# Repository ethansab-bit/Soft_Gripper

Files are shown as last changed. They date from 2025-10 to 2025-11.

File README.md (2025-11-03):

# Whole-Body Proprioceptive Morphing: A Modular Soft Gripper for Robust Cross-Scale Grasping

Official code repository for the paper:  
**"Whole-Body Proprioceptive Morphing: A Modular Soft Gripper for Robust Cross-Scale Grasping"**

## Authors

**Dong Heon Han¹, Xiaohao Xu²†, Yuxi Chen¹, Yusheng Zhou², Xinqi Zhang¹, Jiaqi Wang², Daniel Bruder¹, Xiaonan Huang²***  

¹ *Mechanical Engineering Department, University of Michigan – Ann Arbor, Ann Arbor, MI, USA*  
² *Robotics Department, University of Michigan – Ann Arbor, Ann Arbor, MI, USA*  

† *Project Lead* | * Corresponding Author  

**Emails:**  
- (dongheon, ethansab, dadaaa, dbruder)@umich.edu
- (xiaohaox, yszhou, wangjq, xiaonanh)@umich.edu



## Overview
This repository provides the control and communication code for the modular soft gripper system described in the paper.
The system integrates Arduino-based low-level actuation and a Python control interface for proprioceptive feedback and grasp modulation.

## Repository Structure
```bash
main/
├── Gripper_CAD/                    # CAD files
├── Gripper_FullCode/
│   └── Gripper_FullCode.ino        # Firmware controlling the modular soft gripper
├── GripperControl.py               # Main Python UI and control logic
├── serial_controller.py            # Handles serial communication with Arduino
├── uipic.png                       # UI illustration
├── UserInterfaceDemo.png
├── Schematic_Gripper.png
├── requirements.txt
└── README.md
```

## Clone the Repository
To download or clone this repository:
### Option 1 — Using HTTPS
```bash
git clone https://github.com/ethansab-bit/Soft_Gripper.git
```
### Option 2 — Download ZIP
Click the **Code → Download ZIP** button on GitHub, then unzip the project folder locally.

## Requirements
### Python Environment
- Python ≥ 3.8
- Install required dependencies:
  ```bash
  pip install -r requirements.txt
  ```
### Arduino Environment
- Arduino IDE ≥ 2.0
- Required Libraries:
  1. [Adafruit LPS35HW Library](https://github.com/adafruit/Adafruit_LPS35HW) (Provides the   `Adafruit_LPS35HW.h` header used for pressure sensing)
  2. [Adafruit Sensor Library](https://github.com/adafruit/Adafruit_Sensor) (Dependency required by LPS35HW library)
  
  To install:
    1. Open **Arduino IDE**
    2. Go to **Tools → Manage Libraries...**
    3. Search for **“Adafruit LPS35HW”**
    4. Click **Install** (this will automatically install its dependencies)

## Usage
### System Wiring
The control system requires the following electric devices:
  - Arduino Mega2560 Control Board × 1
  - L298N Motor Driver × 3
  - X605LF Valve × 10
  - LPS3X Pressure Sensor × 4
  - Bending Sensor × 4

The **Arduino Mega2560** should remain connected to the computer **at all times** for communication and control.
All **L298N motor drivers** and bending sensors must be powered by a **5 V** source.

Each bending sensor should be connected in series with a **15 kΩ resistor** to ground. The junction point between the sensor and the resistor should be wired to one of the **analog input ports (A0–A15)** on the Mega2560.

All **VCC pins** of the LPS3X pressure sensors should be connected to the **3.3 V output** on the Mega2560.

The complete wiring layout is illustrated in the diagram below:
<p align="center">
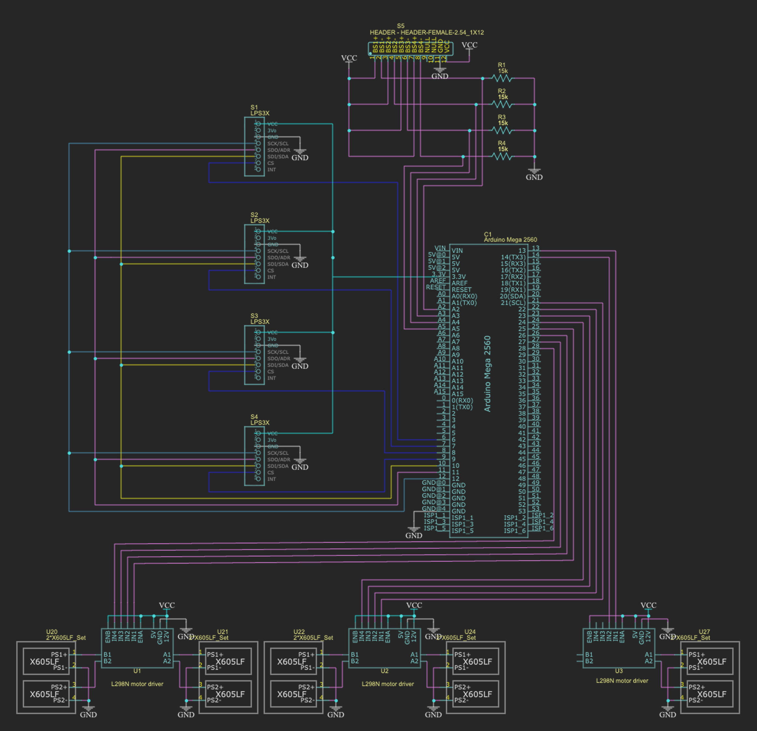
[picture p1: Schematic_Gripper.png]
  
</p>

### Upload the Arduino Code
1. Open `Gripper_FullCode/Gripper_FullCode.ino` in **Arduino IDE**
2. Ensure the **Adafruit_LPS35HW** and **Adafruit_Sensor** libraries are installed
3. Select the correct **Board** and **Port**
4. Click **Upload**

**Notice**: The `Gripper_FullCode.ino` file **must remain inside its folder with the same name** (`Gripper_FullCode/`). Otherwise, the Arduino IDE will not be able to locate dependencies and compile the code.

### Run the Python Control Interface
```bash
python GripperControl.py --port COM4
```
This command launches the UI for controlling the gripper and visualizing proprioceptive (pressure-based) feedback. Make sure to **replace** `COM4` **with the serial port corresponding to your Arduino Control Board**. You can check the active serial port under **Tools → Port** in the **Arduino IDE**. If `--port ...` is omitted, the program will use the default port setting `COM4`.

**Notice**: Before running the Python control program, make sure to **close the Serial Monitor** in the Arduino IDE (or any other application accessing the serial port). **Only one program can use the serial connection at a time**.

### Control Interface Operation
The graphical user interface (GUI) allows users to control and monitor each pneumatic actuator of the soft gripper in real time.  
Each actuator’s target and measured pressure (in hPa) are displayed along with control sliders and state indicators.
<p align="center">
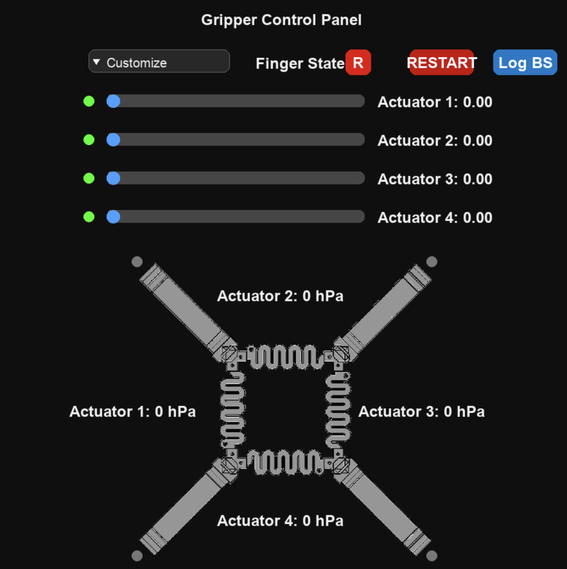
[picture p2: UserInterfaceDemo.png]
  
</p>
Users can:

  - Adjust actuator length using the on-screen sliders (0.00-1.00 extension)
  - Observe real-time sensor readings from **LPS35HW** pressure sensors  
  - Control the gripper finger states (`Finger State` button, `R` for **Release**, `G` for **Gripped**)  
  - Log the data from four bending sensors (`Log BS`). The data will be stored in the same directory as `bend_log.txt`.
  - Recalibrate the actuator (`Restart`). The system will release all air pressure in actuators and fingers and automatically recalibrate to atmospheric pressure within a few seconds.

## CAD Files
All CAD resources for the soft gripper are organized within the repository: Soft_Gripper / Gripper_CAD

## Paper
arxiv: https://arxiv.org/abs/2510.27666

---

## License
This project is licensed under the [MIT License](https://opensource.org/licenses/MIT).

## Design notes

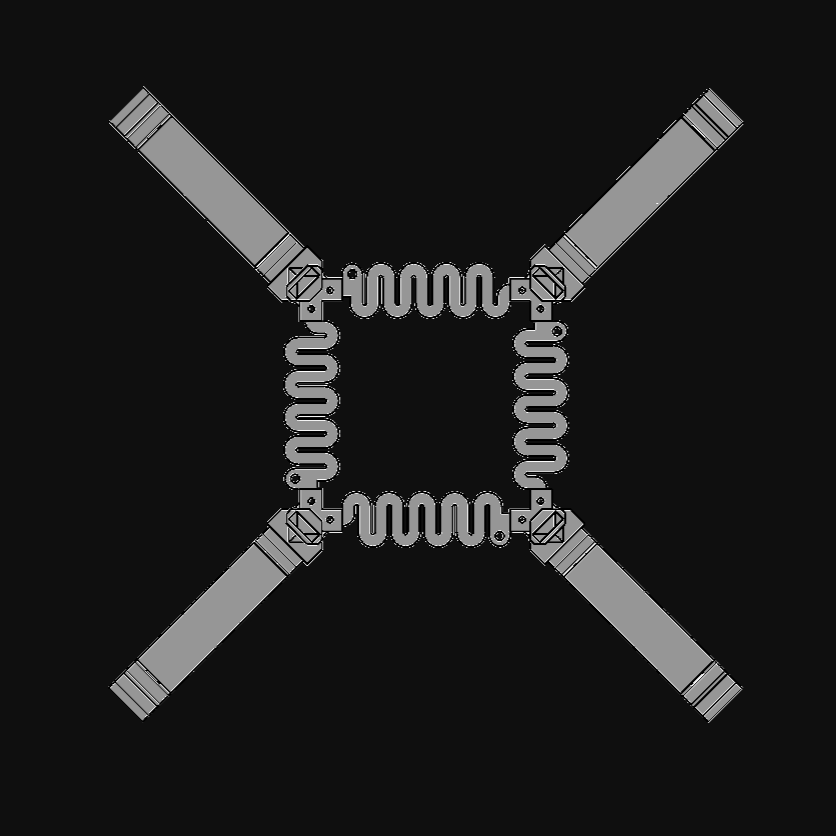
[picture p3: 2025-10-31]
uipic.png

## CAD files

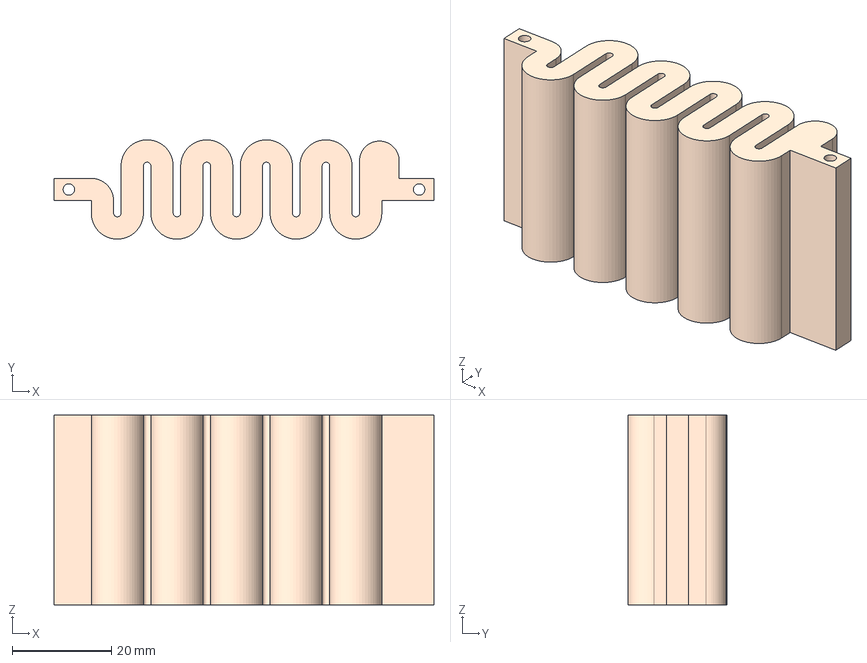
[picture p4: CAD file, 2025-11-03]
Gripper_CAD/Palm.step
76.5 x 20.0 x 38.2 mm

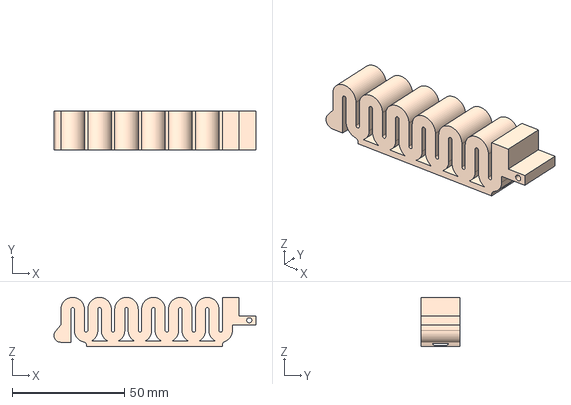
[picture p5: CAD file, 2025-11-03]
Gripper_CAD/Finger.step
90.1 x 17.5 x 22.0 mm

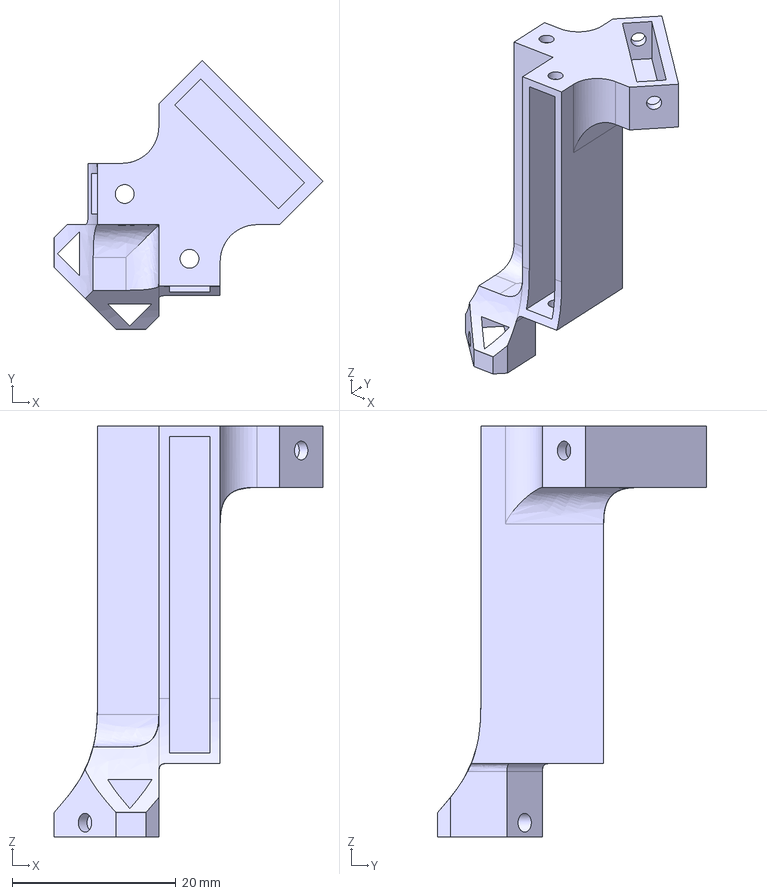
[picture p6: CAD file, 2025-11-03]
Gripper_CAD/bodyConnector.step
32.9 x 32.9 x 50.2 mm

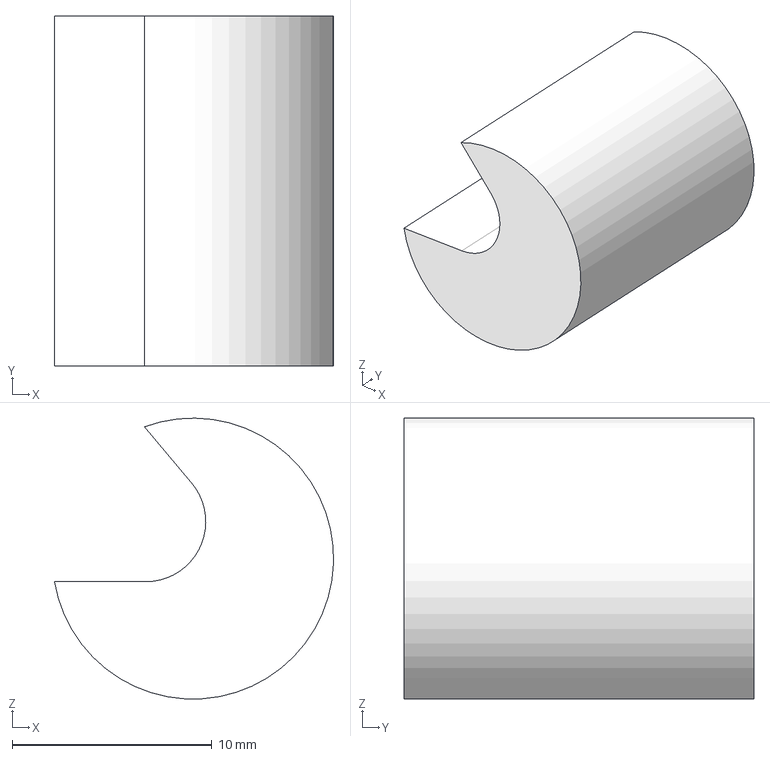
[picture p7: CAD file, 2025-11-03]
Gripper_CAD/Finger Tip.step
14.0 x 17.5 x 14.0 mm

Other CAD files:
Gripper_CAD/Finger Tip.stl
Gripper_CAD/bodyConnector.stl

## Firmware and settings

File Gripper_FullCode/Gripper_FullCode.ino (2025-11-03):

#include <Adafruit_LPS35HW.h>
#include <SPI.h>
#include <math.h>

// Port Declaration
#define SCK 12
#define SDO 11
#define SDI 10
const int CSP[4] = {6, 7, 8, 9};

const int BS[4] = {A2, A3, A4, A5};

const int ActIn[4]  = {22, 24, 26, 28};
const int ActOut[4] = {23, 25, 27, 29};

const int FinIn = 13;
const int FinOut = 14;

// Pressure Sensor
Adafruit_LPS35HW preSensor[4] = {Adafruit_LPS35HW(), Adafruit_LPS35HW(), Adafruit_LPS35HW(), Adafruit_LPS35HW()};

// Time Variable
unsigned long curTime;
unsigned long preTime;
float dt = 0;
float cycleLength = 100;
unsigned long startCycle = 0;
const int finChargeCycle = 10;
const float finChargeProp = 0.5;

// Pressure Variable
float targetPre[4] = {0, 0, 0, 0};
float currentPre[4] = {0, 0 ,0 ,0};
float errorPre[4] = {0, 0, 0, 0};
float atmPre = 0;

// Input Variable
float targetActState[4] = {0, 0, 0, 0};
bool targetFinState = false;

// Output Variable
int gripFlag[4] = {0, 0, 0, 0};
bool stopFlag[4] = {true, true, true, true};
const int gripRange[4] = {82, 46, 47, 23};
const int gripLowLimit[4] = {91, 29, 119, 47};
const float gripThrehold[4] = {.95, .60, .60, .90};

// PID Constant
const float Kp = 0.001;
const float Ki = 0.000003;
const float Kd = 0.000008;

// Control Constant
const float deadLimit = 0.03;
float interval = 1076.0230;

// PID Variable
float integral[4] = {0, 0, 0, 0};
float derivative[4] ={0, 0, 0, 0};
float error[4] = {0, 0, 0, 0};
float preError[4] = {0, 0, 0, 0};
float score[4] = {0, 0, 0, 0};

// Function Declaration
void ReadInput();
void InitialState();
void Len2Pre();
void readCurPre();
void CalcTime();
void CalcPID();
void ControlValve();
void PrintInfo();

void setup() {
  // put your setup code here, to run once:
  Serial.begin(9600); 

  // Initiate Pressure Sensor
  for (int i = 0; i < 4; i++) {
    if (!preSensor[i].begin_SPI(CSP[i], SCK, SDO, SDI)) {
      Serial.print("Invalid Pressure Sensor #");
      Serial.println(i);
      while(1);
    }
  }

  // Initaite the Valve
  for (int i = 0; i < 4; i++) {
    pinMode(ActIn[i], OUTPUT);
    pinMode(ActOut[i], OUTPUT);
  }
  pinMode(FinIn, OUTPUT);
  pinMode(FinOut, OUTPUT);

  // Initiate Time
  curTime = millis();
  preTime = millis();

  InitialState();
}


void loop() {
  // put your main code here, to run repeatedly:
  ReadInput();
  Len2Pre();
  readCurPre();
  readGripFlag();
  CalcTime();
  CalcPID();
  ControlValve();
  PrintInfo();
}

void ReadInput() {
  // Read input from the serial, changing length by "l1 l2 l3 l4", constrol finger by "G" or "R", restart by "S"
  if (Serial.available() > 0) {
    String input = Serial.readStringUntil('\n');
    input.trim();

    if (input == "s" || input == "S") {
      for (int i = 0; i < 4; i++) {
        targetActState[i] = 0;
      }
      targetFinState = false;
      InitialState();
      return;
    }

    if (input == "g" || input == "G") {
      targetFinState = true;
    } else if (input == "r" || input == "R") {
      targetFinState = false;
    }

    float temp[4];
    int index = 0;

    int lastSpace = -1;
    for (int i = 0; i < input.length(); i++) {
      if (input.charAt(i) == ' ' || i == input.length() - 1) {
        int endIdx = (input.charAt(i) == ' ') ? i : i + 1;
        String numStr = input.substring(lastSpace + 1, endIdx);
        numStr.trim();
        if (index < 4) {
          temp[index] = numStr.toFloat();
          index++;
        }
        lastSpace = i;
      }
    }

    if (index == 4) {
      for (int i = 0; i < 4; i++) {
        targetActState[i] = constrain(temp[i], 0.0, 1.2);
      }
    } else {
      Serial.println("Invalid input. Please enter 4 numbers.");
    }
  }
}

void InitialState() {
  // Release all the pressure in fingers & actuators
  for (int i = 0; i < 4; i++) {
    digitalWrite(ActIn[i], LOW);
    digitalWrite(ActOut[i], HIGH);
    delay(1000);
  }
  digitalWrite(FinIn, LOW);
  digitalWrite(FinOut, HIGH);
  delay(1000);

  // Measure & Reset the atmosphere pressure
  float sumPre = 0;
  for (int i = 0; i < 4; i++) {
    for (int j = 0; j < 10; j++) {
      sumPre += preSensor[i].readPressure();
    }
  }
  atmPre = sumPre / 40;
  delay(500);
}

void Len2Pre() {
  // Transfer the length proportion into pressure
  
  for (int i = 0; i < 4; i++) {
    if (targetActState[i] == 0) {
      targetPre[i] = 0;
      continue;
    }
    float targetLength = 70 * (1 + targetActState[i]);
    targetPre[i] = 0.002 * targetLength * targetLength * targetLength - 0.6508 * targetLength * targetLength + 75.6529 * targetLength - 1798.7 - atmPre;
  }
}

void readCurPre() {
  for (int i = 0; i < 4; i++) {
    currentPre[i] = preSensor[i].readPressure() - atmPre;
  }
}

void readGripFlag() {
  if (targetFinState) {
    for (int i = 0; i < 4; i++) {
      if ((float)(analogRead(BS[i]) - gripLowLimit[i])/(float)gripRange[i] < gripThrehold[i]) {
        gripFlag[i] = 1;
      } else {
        gripFlag[i] = -1;
      }
    }
  } else {
    for (int i = 0; i < 4; i++) {
      gripFlag[i] = 0;
    }
  }
}

void CalcTime() {
  // Calculate the derivative time and renew curTime & preTime
  curTime = millis();
  dt = (curTime - preTime) / 1000.0;
  preTime = curTime;
}

void CalcPID() {
  // Calculate PID with constant and variable and return a estimate score from -1 to 1
  for (int i = 0; i < 4; i++) {
    error[i] = targetPre[i] - currentPre[i];
    integral[i] += error[i] * dt;
    derivative[i] = (error[i] - preError[i]) / dt;
    preError[i] = error[i];
    score[i] = constrain(Kp * error[i] + Ki * integral[i] + Kd * derivative[i], -1, 1);
  }
}

void ControlValve() {
  // Control the actuators and fingers using the PID control variables
  unsigned long curTimeTemp = millis();
  unsigned long curCycleTime = curTimeTemp - startCycle;

  if (curCycleTime >= cycleLength) {
    startCycle = curTimeTemp;
    curCycleTime = 0;
  }

  for (int i = 0; i < 4; i++) {
    if (score[i] > deadLimit && curCycleTime < fabs(score[i]) * cycleLength) {
      digitalWrite(ActIn[i], HIGH);
      digitalWrite(ActOut[i], LOW);
      stopFlag[i] = false;
    } else if (score[i] < -deadLimit && curCycleTime < fabs(score[i]) * cycleLength) {
      digitalWrite(ActIn[i], LOW);
      digitalWrite(ActOut[i], HIGH);
      stopFlag[i] = false;
    } else {
      digitalWrite(ActIn[i], LOW);
      digitalWrite(ActOut[i], LOW);
      if (score[i] >= -deadLimit && score[i] <= deadLimit) {
        integral[i] = 0;
        stopFlag[i] = true;
      }
    }
  }

  if (targetFinState) {
    digitalWrite(FinIn, HIGH);
    digitalWrite(FinOut, LOW);
  } else {
    digitalWrite(FinIn, LOW);
    digitalWrite(FinOut, HIGH);
  }

}

void PrintInfo() {
  // Print the state of the gripper
  for (int i = 0; i < 4; i++) {
    Serial.print(currentPre[i] + atmPre);
    Serial.print(" ");
  }
  for (int i = 0; i < 4; i++) {
    if (stopFlag[i]) {
      Serial.print("T");
    } else {
      Serial.print("F");
    }
    Serial.print(" ");
  }
  for (int i = 0; i < 4; i++) {
    Serial.print(gripFlag[i]);
    Serial.print(" ");
  }
  for (int i = 0; i < 4; i++) {
      Serial.print(analogRead(BS[i]));
      Serial.print(" ");
  }
  Serial.println();

}

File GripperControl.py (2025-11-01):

import pygame
import pygame.gfxdraw
import math
import os
import sys
import time
import argparse
from serial_controller import SerialController

def main():
    parser = argparse.ArgumentParser(description="Gripper Control Panel")
    parser.add_argument("--port", type=str, default="COM4",
                        help="Serial port for Arduino connection (e.g. COM3 or /dev/cu.usbmodem101)")
    args = parser.parse_args()

    sc = SerialController(args.port)
    print(f"Connected to serial port: {args.port}")

# ===== Color Theme =====
COLOR_BG         = (15, 15, 15)
COLOR_CARD_BG    = (30, 30, 30)
COLOR_TRACK      = (70, 70, 70)
COLOR_KNOB       = (60, 160, 255)
COLOR_TRACK_HL   = (120, 120, 120)
COLOR_TEXT       = (240, 240, 240)

COLOR_BTN_G      = (0, 168, 84)
COLOR_BTN_R      = (230, 0, 0)
COLOR_BTN_LABEL  = (255, 255, 255)

MODEL_BTN_BG     = (40, 40, 40)
MODEL_BTN_BORDER = (100, 100, 100)
MODEL_BTN_TEXT   = (240, 240, 240)

COLOR_PANEL_BG           = (45, 45, 45)
COLOR_PANEL_ITEM         = (60, 60, 60)
COLOR_PANEL_ITEM_HOVER   = (80, 80, 80)

COLOR_IND_X = (120, 120, 120)   
COLOR_IND_T = (0, 255, 0)     
COLOR_IND_F = (255, 0, 0)     

# ===== UI POSITION =====
WIN_W, WIN_H = 900, 900
SLIDER_X, SLIDER_W = 180, 400
SLIDER_TOP, SLIDER_SPACING, SLIDER_H = 150, 60, 20
ACTPOS = [[100, 630], [330, 450], [550, 630], [330, 800]]

BEND_BTN_RECT = pygame.Rect(780, 80, 100, 40)
bend_pressed = False
logging_bend = False
bend_file = None


KNOB_MARGIN = 8

FLAG_BOX_RECT = pygame.Rect(550, 80, 40, 40)
MODEL_BTN_RECT = pygame.Rect(150, 80, 220, 36)
MODEL_ITEM_H = 30
MODEL_DROPDOWN_X = MODEL_BTN_RECT.x
MODEL_DROPDOWN_Y = MODEL_BTN_RECT.bottom + 4
MODEL_DROPDOWN_W = MODEL_BTN_RECT.width
STOP_BTN_RECT = pygame.Rect(650, 80, 100, 40)

GRIP_CENTER = [[225, 410], [684, 410], [684, 868], [225, 868]]

# ===== Initialize Pygame =====
pygame.init()
screen = pygame.display.set_mode((WIN_W, WIN_H))
pygame.display.set_caption("Arduino Controller")
FONT_NAME = "Calibri"
FONT_SIZE_LARGE = 24
FONT_SIZE_SMALL = 20
font = pygame.font.SysFont(FONT_NAME, FONT_SIZE_LARGE)
bold_font = pygame.font.SysFont(FONT_NAME, FONT_SIZE_LARGE, bold=True)
small_font = pygame.font.SysFont(FONT_NAME, FONT_SIZE_SMALL)

# ===== Initialize Variable =====
curPre = [0, 0, 0, 0]
stopFlag = ['T', 'T', 'T', 'T']
graspFlag = [0, 0, 0, 0]


values = [0.0, 0.0, 0.0, 0.0]
flag = 'R'
dragging_index = None
panel_open = False
current_preset_name = "Customize"
preset_item_rects = {}

flag_pressed = False
stop_pressed = False
model_pressed = False
slider_pressed = [False, False, False, False]
PRESETS = {
    "Square Small":    [0.0, 0.0, 0.0, 0.0],
    "Square Large":    [0.8, 0.8, 0.8, 0.8],
    "Trapezoid Small": [1.0, 0.0, 0.0, 0.0],
    "Trapezoid Large": [1.0, 1.0, 1.0, 0.0],
    "Kite":            [1.0, 1.0, 0.0, 0.0],
    "Rectangle":       [1.0, 0.0, 1.0, 0.0],
    "Advocado":        [0.0, 0.5, 0.0, 0.5],
}


def match_preset(val_list):
    for name, preset in PRESETS.items():
        if all(math.isclose(a, b, abs_tol=1e-3) for a, b in zip(val_list, preset)):
            return name
    return "Customize"

def set_values_and_send(new_vals):
    global values, current_preset_name
    values = [max(0.0, min(1.0, float(v))) for v in new_vals]
    sc.sendActState(values)
    current_preset_name = match_preset(values)


def get_slider_index(mx, my):
    for i in range(4):
        y = SLIDER_TOP + i * SLIDER_SPACING
        if y <= my <= y + SLIDER_H and SLIDER_X <= mx <= SLIDER_X + SLIDER_W:
            return i
    return None

def draw_bend_button():
    global bend_pressed, logging_bend
    mouse_pos = pygame.mouse.get_pos()
    is_hovered = BEND_BTN_RECT.collidepoint(mouse_pos)
    base_color = (0, 120, 200)
    hover_color = (0, 150, 240) if is_hovered else base_color

    rect = BEND_BTN_RECT.inflate(4, 4) if bend_pressed else BEND_BTN_RECT
    pygame.draw.rect(screen, hover_color, rect, border_radius=10)
    label_text = "Stop Log" if logging_bend else "Log BS"
    label = bold_font.render(label_text, True, (255, 255, 255))
    text_rect = label.get_rect(center=rect.center)
    screen.blit(label, text_rect)


def draw_title_bar():
    title = bold_font.render("Gripper Control Panel", True, COLOR_TEXT)
    screen.blit(title, (WIN_W // 2 - title.get_width() // 2, 20))

def draw_slider(index, value):
    x = SLIDER_X
    y = SLIDER_TOP + index * SLIDER_SPACING

    knob_min_x = x + KNOB_MARGIN
    knob_max_x = x + SLIDER_W - KNOB_MARGIN
    knob_x = int(knob_min_x + value * (knob_max_x - knob_min_x))
    knob_y = y + SLIDER_H // 2

    pygame.draw.rect(screen, COLOR_TRACK, (x, y, SLIDER_W, SLIDER_H), border_radius=8)

    filled_width = knob_x - x
    if filled_width > 0:
        pygame.draw.rect(screen, COLOR_TRACK_HL, (x, y, filled_width, SLIDER_H), border_radius=8)

    knob_radius = 12 if slider_pressed[index] else 10
    pygame.gfxdraw.filled_circle(screen, knob_x, knob_y, knob_radius, COLOR_KNOB)
    pygame.gfxdraw.aacircle(screen, knob_x, knob_y, knob_radius, COLOR_KNOB)

    label = bold_font.render(f"Actuator {index + 1}: {value:.2f}", True, COLOR_TEXT)
    screen.blit(label, (x + SLIDER_W + 20, y - 2))

def draw_flag_button(flag_state):
    global flag_pressed
    label = bold_font.render("Finger State:", True, COLOR_TEXT)
    screen.blit(label, (FLAG_BOX_RECT.x - 140, FLAG_BOX_RECT.y + 8))

    mouse_pos = pygame.mouse.get_pos()
    is_hovered = FLAG_BOX_RECT.collidepoint(mouse_pos)
    color = COLOR_BTN_G if flag_state == 'G' else COLOR_BTN_R
    if is_hovered:
        color = tuple(min(255, c + 30) for c in color)

    rect = FLAG_BOX_RECT.inflate(4, 4) if flag_pressed else FLAG_BOX_RECT
    pygame.draw.rect(screen, color, rect, border_radius=10)
    text = bold_font.render(flag_state, True, COLOR_BTN_LABEL)
    text_rect = text.get_rect(center=rect.center)
    screen.blit(text, text_rect)

def draw_stop_button():
    global stop_pressed
    mouse_pos = pygame.mouse.get_pos()
    is_hovered = STOP_BTN_RECT.collidepoint(mouse_pos)
    base_color = (200, 0, 0)
    hover_color = (230, 50, 50) if is_hovered else base_color

    rect = STOP_BTN_RECT.inflate(4, 4) if stop_pressed else STOP_BTN_RECT
    pygame.draw.rect(screen, hover_color, rect, border_radius=10)
    label = bold_font.render("RESTART", True, (255, 255, 255))
    text_rect = label.get_rect(center=rect.center)
    screen.blit(label, text_rect)
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

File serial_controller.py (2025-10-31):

import serial
import time

class SerialController:
    def __init__(self, port='COM4', baudrate=9600):
        self.ser = serial.Serial(port, baudrate, timeout=1)
        time.sleep(2)
        print(f"Connected to {port} at {baudrate} baud")

    def sendActState(self, actState):
        assert len(actState) == 4
        msg = f"{actState[0]:.2f} {actState[1]:.2f} {actState[2]:.2f} {actState[3]:.2f}\n"
        self.ser.write(msg.encode())
        print("Send Actuator State: ", msg.strip())

    def sendFinState(self, finState):
        assert finState in ['G', 'R']
        msg = f"{finState}\n"
        self.ser.write(msg.encode())
        print("Sent Finger State: ", msg.strip())

    def readOutput(self):
        if self.ser.in_waiting > 0:
            try:
                line = self.ser.readline().decode('utf-8').strip()
                parts = line.split()

                if len(parts) == 12:
                    curPre = list(map(float, parts[:4]))
                    stopFlag = parts[4:8]
                    graspFlag = parts[8:12]
                    return curPre, stopFlag, graspFlag, None

                if len(parts) == 16:
                    curPre = list(map(float, parts[:4]))
                    stopFlag = parts[4:8]
                    graspFlag = parts[8:12]
                    bendVals = list(map(int, parts[12:16]))
                    return curPre, stopFlag, graspFlag, bendVals

            except Exception as e:
                print("[Serial Parse Error]", e)
        return None, None, None, None



    def close(self):
        self.ser.close()

        print("Serial connection closed.")

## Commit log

2025-10-31 Add initial Gripper_FullCode.ino file
2025-10-31 Update README with installation steps for library
    Added installation instructions for Adafruit PWM Servo Driver Library.
2025-10-31 Enhance README with Arduino and usage instructions
    Updated Arduino environment setup instructions and added usage details for the Python control interface.
2025-10-31 Add confirmation message on serial connection close
    Added a print statement to confirm closure of the serial connection.
2025-10-31 Add command-line argument parsing and refactor main loop
    Refactor GripperControl.py to include command-line argument parsing for the serial port and restructure the main loop.
2025-10-31 Enhance README with GUI control interface details
    Added details about the GUI for controlling pneumatic actuators and monitoring sensor readings.
2025-11-03 Update pin definitions for Gripper control
2025-11-03 Update README with system wiring details
    Added wiring requirements and details for control system components.
2025-11-03 Update README with wiring instructions and diagram
    Added wiring instructions and image for sensors.
2025-11-03 Fix command path for GripperControl.py
    Updated the command to run the Python Control Interface by removing the 'Python/' prefix.
2025-11-03 Add schematic image to README
2025-11-03 Document actuator recalibration process
    Added recalibration feature for the actuator.
2025-11-03 Add CAD files section to README
    Added section for CAD files in the README.
